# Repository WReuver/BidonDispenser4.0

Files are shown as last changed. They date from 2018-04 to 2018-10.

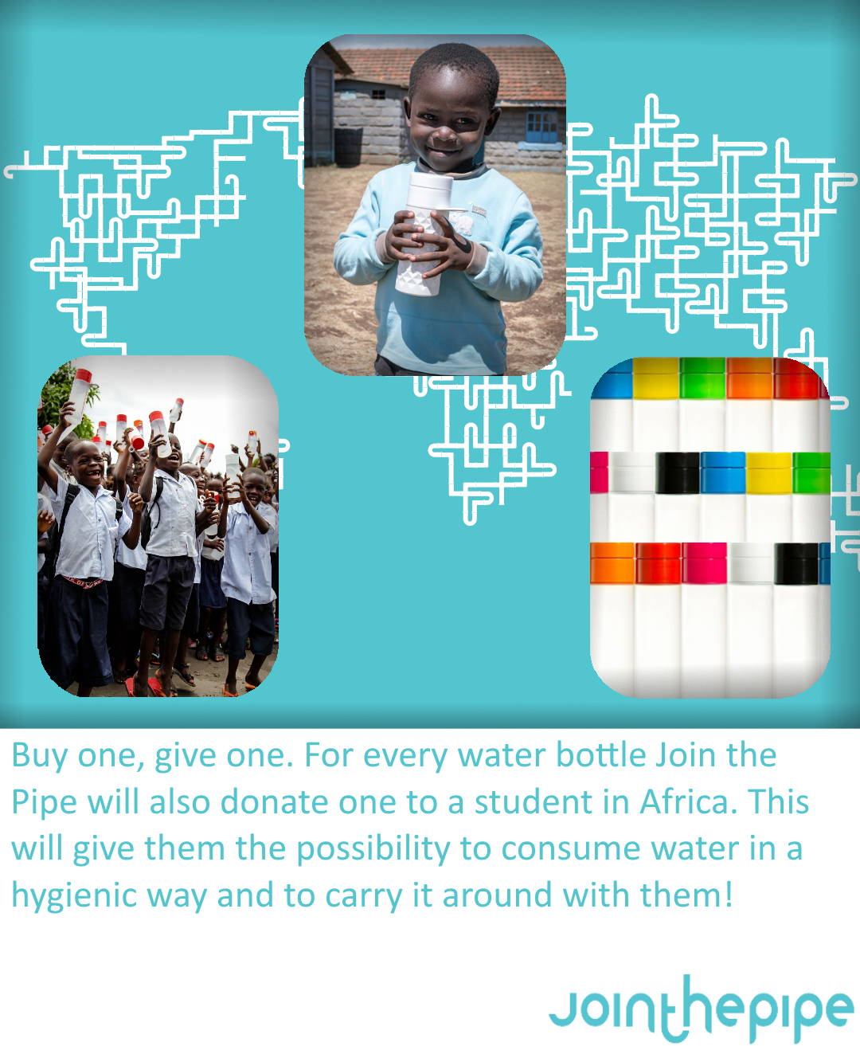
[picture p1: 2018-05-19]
RaspberryPi/Software/BidonDispenser/BidonDispenser/Assets/Images/Promotions/BuyOneGiveOne.png

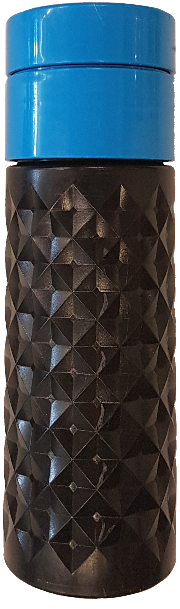
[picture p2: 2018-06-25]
RaspberryPi/Software/BidonDispenser/BidonDispenser/Assets/Images/BottleColours/B_BlueBottle.png

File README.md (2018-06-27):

# Bidon Dispenser 4.0
_Smart Solutions Semester - Join the Pipe - Year 17/18 - Semester 02_

### Authors
All the software is written by Robin C. Pel with student number 421 431. 
All the hardware is designed by Glen te Hofsté with student number 419 720. 

### Note to self
Use "git merge --allow-unrelated-histories [ORPHAN-BRANCH]" to merge orphan branches.

### While Loops
All the while loops in the Microcontroller's program:
- "./Communication/OneWire.cpp" line 13: Wait for a pin to be high
- "./Communication/USART.cpp" line 34: Wait for new data on the serial port
- "./Communication/USART.cpp" line 42: Wait for new data on the serial port for 2 seconds
- "./Hardware/SystemClock.cpp" line 13: Wait for the clock source to be ready
- "./Master/RaspberryPi.cpp" line 36: Wait until the pre-amble is found
- "./Sensors/DistanceSensor.cpp" line 93: Wait for a pin to be high
- "./Sensors/DistanceSensor.cpp" line 93: Wait for a pin to be low
- "./Sensors/TemperatureSensor.cpp" line 33: Wait for a pin to be high
- "./main.cpp" line 197, 280, 323, 362 and 384: Infinite loops

### Important
Not all code on the "microcontroller/software/develop" branch works with all the microcontroller hardware:  
	- All the commits **BEFORE** the tag "MCU_Festival" only work on the controller PCB v1.1  
	- All the commits **AFTER** the tag "MCU_Festival" only work on the controller PCB v2.0  
  
Another thing that's definitely worth mentioning is that on the microcontroller PCB v1.1 the ADC was used to read a 1 or 0.
This was done because for some weird reason it was not possible to read one of the digital pins, 
the microcontroller probably was broken or something but the decision was made to work around it for the time being.  
  
After the Smart Solutions Festival one of the distance sensors broke, this sensor was distance sensor number five.  
Distance Sensor Layout Layout (Top view, from the front):  
_Dist Sensor: [08] [01] [10] [03] [12] [05] [14] [07]_  
_Dist Sensor: [00] [09] [02] [11] [04] [13] [06] [15]_  

### Disclaimer
This was my first experience with C# and the Visual Studio IDE, there are probably a lot of things which could be optimized. 
This git repo was also misused a little bit, apologies. 
There is _no_ easter egg. 

### Regarding the UI Assets
All UI Assets were made using Paint dot net, you can get it here https://www.dotpdn.com/downloads/pdn.html

### The Team 💪
! The Team 💪

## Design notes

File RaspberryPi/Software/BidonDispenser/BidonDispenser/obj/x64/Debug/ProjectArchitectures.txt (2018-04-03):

C:\Git\BidonDispenser4.0\RaspberryPi\Software\BidonDispenser\BidonDispenser\BidonDispenser.csproj;x64

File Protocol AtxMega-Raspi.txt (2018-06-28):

==============================================================================================================================================
	Dictionary
==============================================================================================================================================
MASTER						= Raspberry Pi
SLAVE						= Micro Controller
LENGTH						= Length of the payload
COLUMNNUMBER 				= 0 ~ 7
EMPTY STATUS OF ALL COLUMNS	= 0b76543210, each bit indicates if a column is empty or not (0b00100111 => column 0, 1, 2 and 5 are empty)
NEW EMPTY DISTANCE			= From which distance the column will be seen as empty
LOWER TARGET TEMEPRATURE	= Which lower temperature the machine should aim for
==============================================================================================================================================

==============================================================================================================================================
	Protocol Format
==============================================================================================================================================
[PREAMBLE0] [PREAMBLE1] [COMMAND] [PARAMETER-LENGTH] [PARAMATERS]

PREAMBLE0			= 0x00
PREAMBLE1			= 0xFF
COMMAND				= See "Command Overview"
PARAMETER-LENGTH 	= Amount of parameters
PARAMATERS			= See "Command Overview"
==============================================================================================================================================

==============================================================================================================================================
	Command Overview
==============================================================================================================================================
COMMANDNAME: 		Lock
DESCRIPTION:		Locks all functionalities until unlocked
MASTER COMMAND:		[0x02]
MASTER PARAMETERS:	-
SLAVE COMMAND:		[0x03]
SLAVE PARAMETERS:	-

COMMANDNAME: 		Unlock
DESCRIPTION:		Unlocks all functionalities if locked
MASTER COMMAND:		[0x04]
MASTER PARAMETERS:	-
SLAVE COMMAND:		[0x05]
SLAVE PARAMETERS:	-

COMMANDNAME: 		Sense
DESCRIPTION:		A check used to sense whether the microcontroller is connected or not
MASTER COMMAND:		[0x06]
MASTER PARAMETERS:	-
SLAVE COMMAND:		[0x07]
SLAVE PARAMETERS:	[0xAB] [0xBC] [0xCD] [0xDA]

COMMANDNAME: 		Temperature
DESCRIPTION:		Command the slave to return the three temperature values
MASTER COMMAND:		[0x08]
MASTER PARAMATERS:	[LOWER TARGET TEMEPRATURE * 2]
SLAVE COMMAND:		[0x09]
SLAVE PARAMETERS:	[LOWER TEMPERATURE * 2] [MIDDLE TEMPERATURE * 2] [UPPER TEMPERATURE * 2]

COMMANDNAME: 		Dispense
DESCRIPTION:		Command the slave to dispense a bidon from the given column and to return the distance of the given column
MASTER COMMAND:		[0x0A]
MASTER PARAMETERS:	[COLUMN-NUMBER]
SLAVE COMMAND:		[0x0B]
SLAVE PARAMETERS:	[EMPTY STATUS OF ALL COLUMNS]

COMMANDNAME: 		Distance
DESCRIPTION:		Command the slave to return all column distances
MASTER COMMAND:		[0x0C]
MASTER PARAMETERS:	[NEW EMPTY DISTANCE (optional)]
SLAVE COMMAND:		[0x0D]
SLAVE PARAMETERS:	[EMPTY STATUS OF ALL COLUMNS]
==============================================================================================================================================

==============================================================================================================================================
	Slave Exceptions 
==============================================================================================================================================
ERRORNAME:			TimeOutError
SLAVE COMMAND:		[0xE0]
SLAVE PARAMETERS:	-

ERRORNAME:			UnknownCommandError
SLAVE COMMAND:		[0xE1]
SLAVE PARAMETERS:	-

ERRORNAME:			NotEnoughParameters
SLAVE COMMAND:		[0xE2]
SLAVE PARAMETERS:	-

ERRORNAME:			Locked
SLAVE COMMAND:		[0xE3]
SLAVE PARAMETERS:	-
==============================================================================================================================================

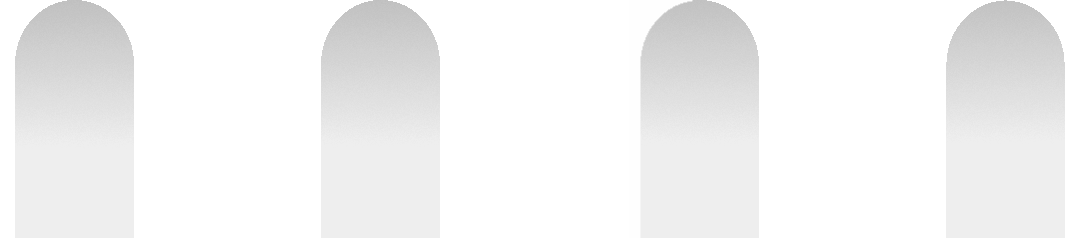
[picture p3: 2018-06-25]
RaspberryPi/Software/BidonDispenser/BidonDispenser/Assets/Images/Selections/FourBottleSelectionType1.png

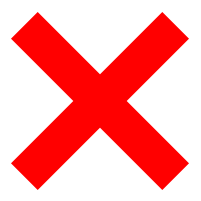
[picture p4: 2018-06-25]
RaspberryPi/Software/BidonDispenser/BidonDispenser/Assets/Images/Misc/RedX2.png

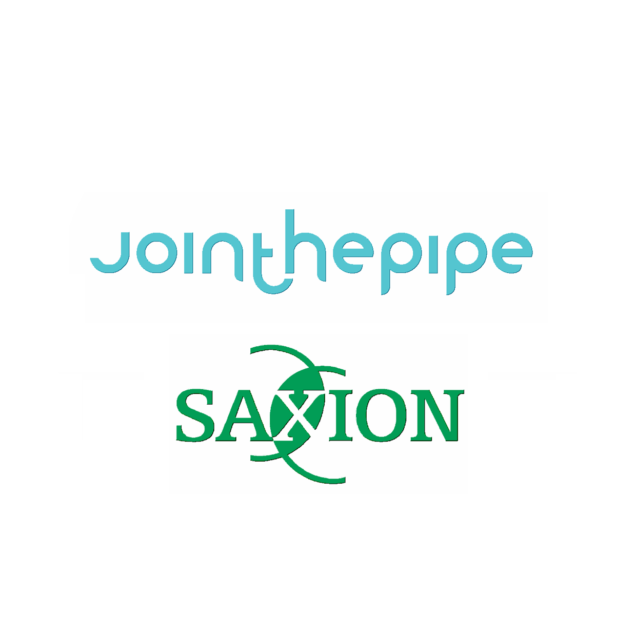
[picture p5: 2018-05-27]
RaspberryPi/Software/BidonDispenser/BidonDispenser/Assets/VisualAssets/LargeTile.scale-400.png

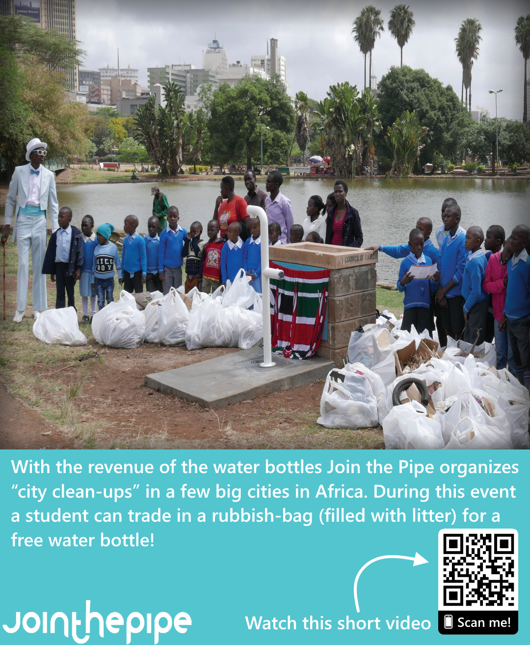
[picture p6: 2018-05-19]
RaspberryPi/Software/BidonDispenser/BidonDispenser/Assets/Images/Promotions/CleanUp.png

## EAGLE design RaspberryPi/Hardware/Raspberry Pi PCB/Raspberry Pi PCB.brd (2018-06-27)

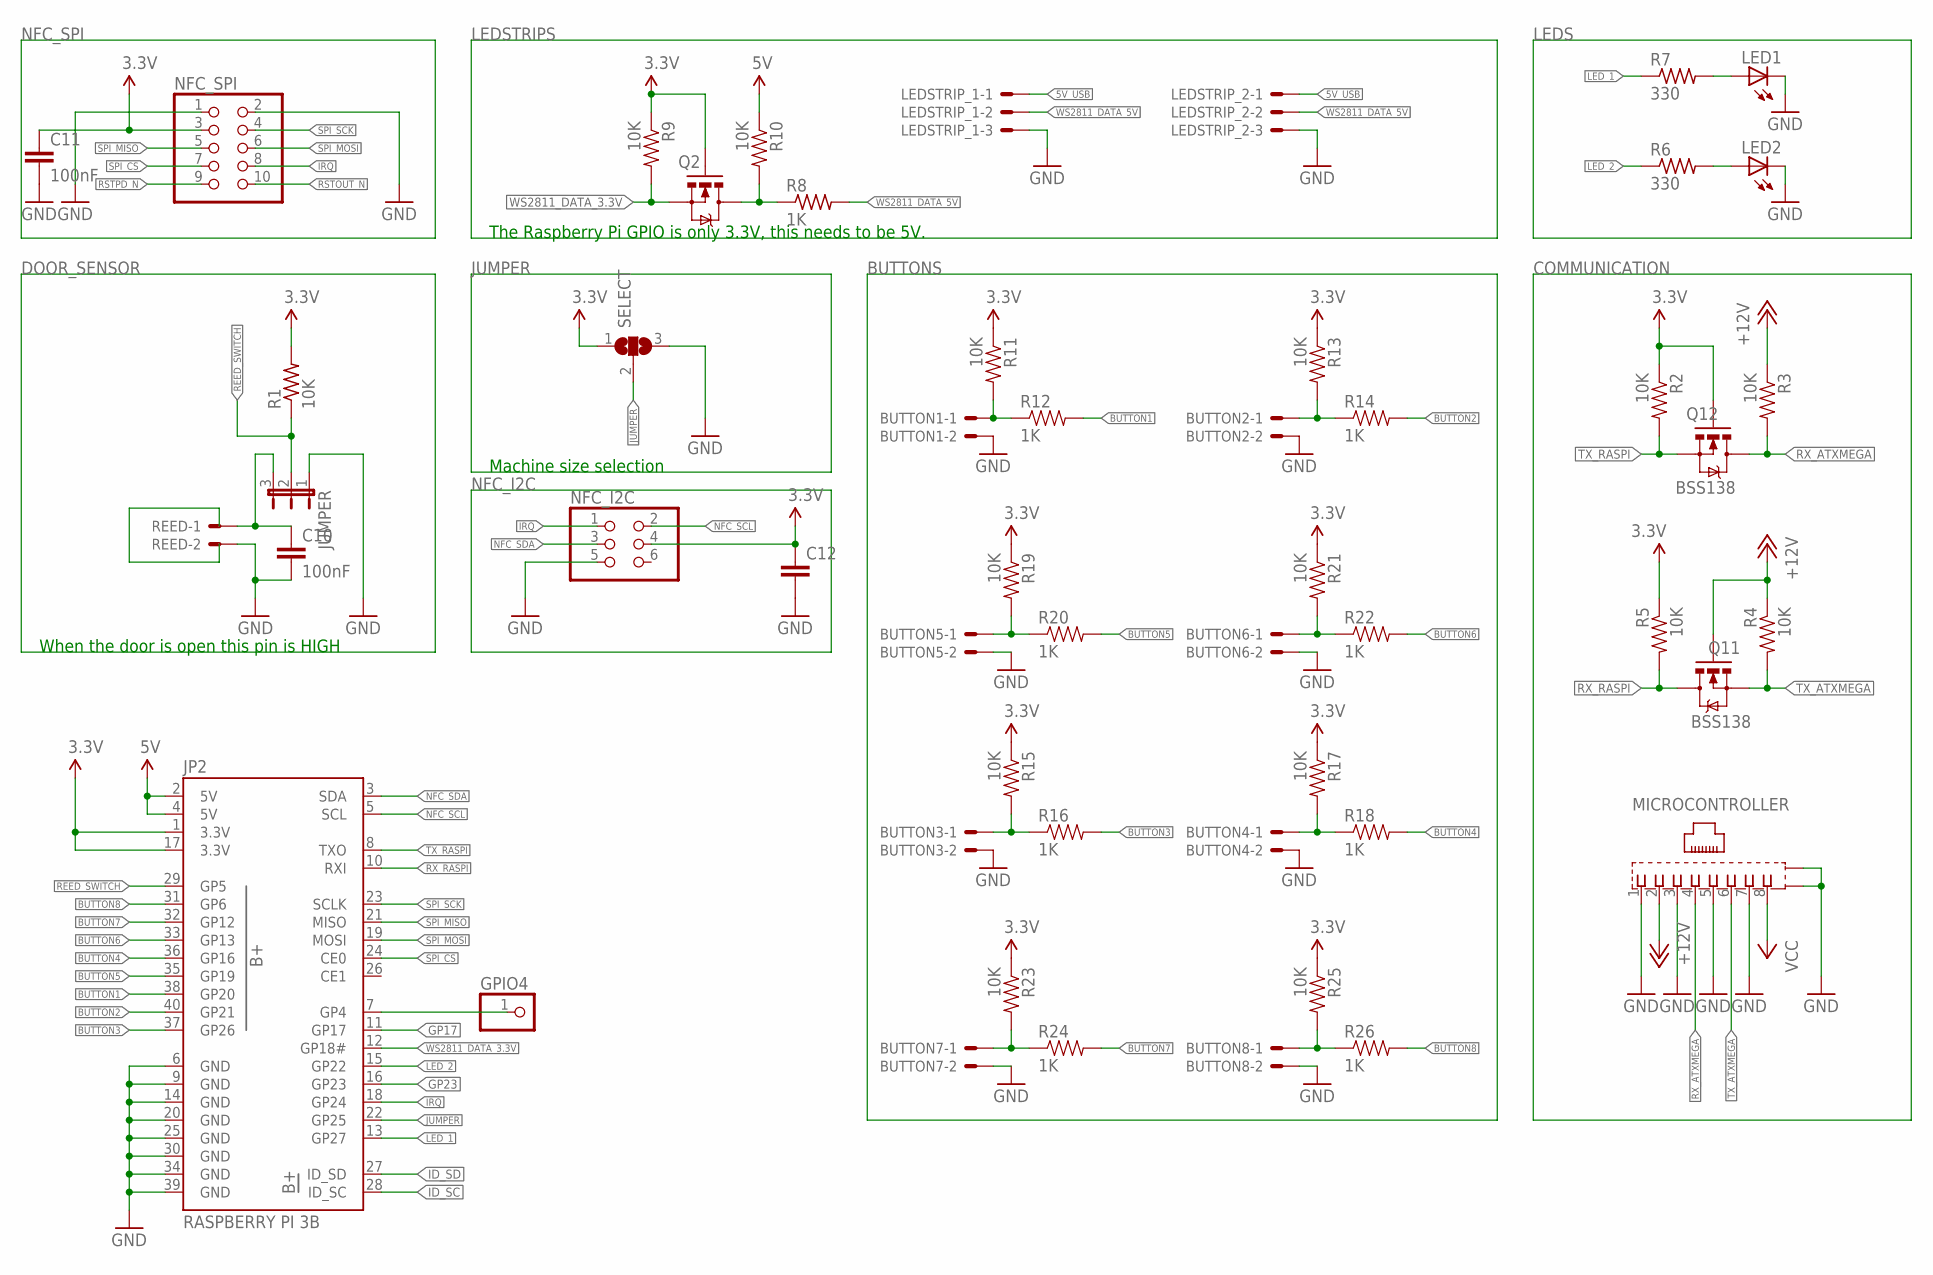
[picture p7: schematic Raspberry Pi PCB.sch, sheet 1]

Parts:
BUTTON1, BUTTON2, BUTTON3, BUTTON4, BUTTON5, BUTTON6, BUTTON7, BUTTON8: 22-05-7028-02; 7395-02
C10, C11, C12: 100nF; 0805
GPIO4: PINHD-1X1; 1X01
JP2: RASPBERRY PI 3B; 2X20-SHROUDED
JUMPER: JP2E; JP2
LED1, LED2: LEDCHIPLED_0805; CHIPLED_0805
LEDSTRIP_1, LEDSTRIP_2: 22-05-7038-03; 7395-03
MICROCONTROLLER: 0446200002
NFC_I2C: PINHD-2X3; 2X03
NFC_SPI: PINHD-2X5; 2X05
Q2, Q11, Q12: BSS138; SOT23-3
R1: 10K; R0805
R2, R3, R4, R5, R9, R10, R11, R13, R15, R17, R19, R21, R23, R25: 10K; 0603-RES
R6, R7: 330; R0805
R8: 1K; R0805
R12, R14, R16, R18, R20, R22, R24, R26: 1K; 0603-RES
REED: 22-05-7028-02; 7395-02
SELECT: SJ2W; SJ_2

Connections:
3.3V: C11.1, C12.1, JP2.1 (3.3V), JP2.17 (3.3V), NFC_I2C.4, NFC_SPI.3, Q2.1 (G), Q12.1 (G), R1.2, R2.1, R5.1, R9.1, R11.1, R13.1, R15.1, R17.1, R19.1, R21.1, R23.1, R25.1, SELECT.1
5V: JP2.2 (5V), JP2.4 (5V), R10.1; also elsewhere on the board
5V_USB: LEDSTRIP_1.1, LEDSTRIP_2.1; also elsewhere on the board
+12V: MICROCONTROLLER.2, Q11.1 (G), R3.1, R4.1
BUTTON1: JP2.38 (GP20), R12.2
BUTTON2: JP2.40 (GP21), R14.2
BUTTON3: JP2.37 (GP26), R16.2
BUTTON4: JP2.36 (GP16), R18.2
BUTTON5: JP2.35 (GP19), R20.2
BUTTON6: JP2.33 (GP13), R22.2
BUTTON7: JP2.32 (GP12), R24.2
BUTTON8: JP2.31 (GP6), R26.2
GND: BUTTON1.2, BUTTON2.2, BUTTON3.2, BUTTON4.2, BUTTON5.2, BUTTON6.2, BUTTON7.2, BUTTON8.2, C10.2, C11.2, C12.2, JP2.6 (GND), JP2.9 (GND), JP2.14 (GND), JP2.20 (GND), JP2.25 (GND), JP2.30 (GND), JP2.34 (GND), JP2.39 (GND), JUMPER.1, LED1.C, LED2.C, LEDSTRIP_1.3, LEDSTRIP_2.3, MICROCONTROLLER.1, MICROCONTROLLER.3, MICROCONTROLLER.5, MICROCONTROLLER.7, MICROCONTROLLER.S@1 (S1), MICROCONTROLLER.S@2 (S2), NFC_I2C.5, NFC_SPI.1, NFC_SPI.2, REED.2, SELECT.3; also elsewhere on the board
GP4: GPIO4.1, JP2.7 (GP4)
GP17: JP2.11 (GP17)
GP23: JP2.16 (GP23)
ID_SC: JP2.28 (ID_SC)
ID_SD: JP2.27 (ID_SD)
IRQ: JP2.18 (GP24), NFC_I2C.1, NFC_SPI.8
JUMPER: JP2.22 (GP25), SELECT.2
LED_1: JP2.13 (GP27), R7.1
LED_2: JP2.15 (GP22), R6.1
unnamed: C10.1, JUMPER.3, REED.1
unnamed: BUTTON2.1, R13.2, R14.1
unnamed: Q2.3 (D), R8.1, R10.2
unnamed: LED2.A, R6.2
unnamed: LED1.A, R7.2
unnamed: BUTTON1.1, R11.2, R12.1
unnamed: BUTTON3.1, R15.2, R16.1
unnamed: BUTTON4.1, R17.2, R18.1
unnamed: BUTTON5.1, R19.2, R20.1
unnamed: BUTTON6.1, R21.2, R22.1
unnamed: BUTTON7.1, R23.2, R24.1
unnamed: BUTTON8.1, R25.2, R26.1
NFC_SCL: JP2.5 (SCL), NFC_I2C.2
NFC_SDA: JP2.3 (SDA), NFC_I2C.3
REED_SWITCH: JP2.29 (GP5), JUMPER.2, R1.1
RSTOUT_N: NFC_SPI.10
RSTPD_N: NFC_SPI.9
RX_ATXMEGA: MICROCONTROLLER.4, Q12.3 (D), R3.2
RX_RASPI: JP2.10 (RXI), Q11.3 (D), R5.2
SPI_CS: JP2.24 (CE0), NFC_SPI.7
SPI_MISO: JP2.21 (MISO), NFC_SPI.5
SPI_MOSI: JP2.19 (MOSI), NFC_SPI.6
SPI_SCK: JP2.23 (SCLK), NFC_SPI.4
TX_ATXMEGA: MICROCONTROLLER.6, Q11.2 (S), R4.2
TX_RASPI: JP2.8 (TXO), Q12.2 (S), R2.2
VCC: MICROCONTROLLER.8
WS2811_DATA_3.3V: JP2.12 (GP18#), Q2.2 (S), R9.2
WS2811_DATA_5V: LEDSTRIP_1.2, LEDSTRIP_2.2, R8.2

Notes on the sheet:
Machine size selection
When the door is open this pin is HIGH
The Raspberry Pi GPIO is only 3.3V, this needs to be 5V.

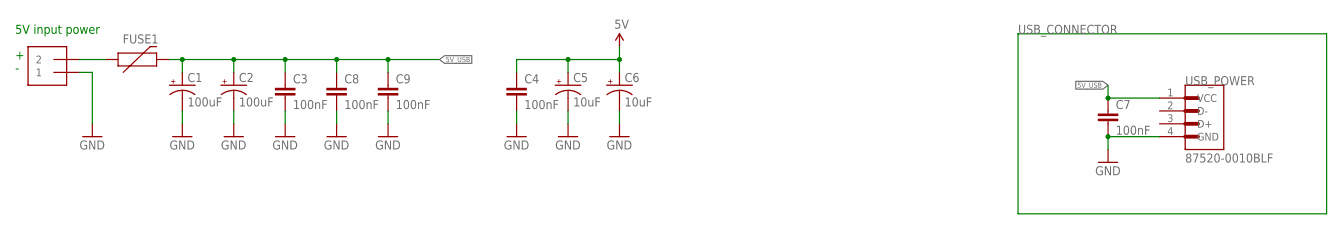
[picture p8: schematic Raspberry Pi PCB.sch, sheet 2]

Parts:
C1, C2: 100uF; 175TMP-0810
C3, C4, C7, C8, C9: 100nF; 0805
C5, C6: 10uF; 153CLV-0505
FUSE1: 6V/0.5A; 1206
INPUT: 1X2-3.5MM
USB_POWER: 87520-0010BLF; FCI_87520-0010BLF

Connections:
5V: C4.1, C5.+, C6.+; also elsewhere on the board
5V_USB: C1.+, C2.+, C3.1, C7.1, C8.1, C9.1, FUSE1.2, USB_POWER.1 (VCC); also elsewhere on the board
GND: C1.-, C2.-, C3.2, C4.2, C5.-, C6.-, C7.2, C8.2, C9.2, INPUT.1, USB_POWER.4 (GND); also elsewhere on the board
VIN1: FUSE1.1, INPUT.2

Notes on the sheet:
5V input power

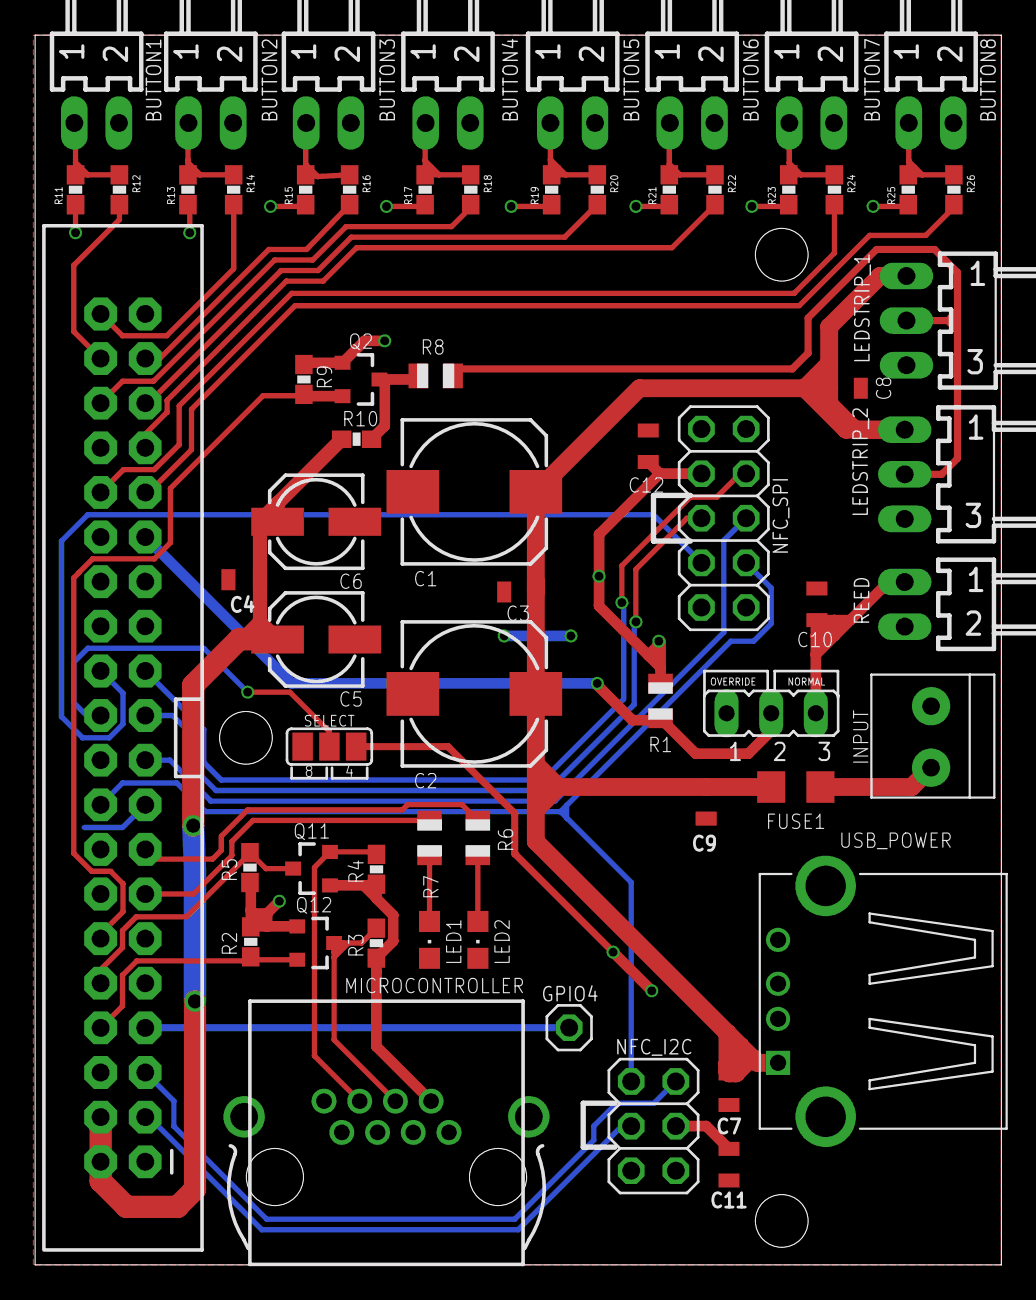
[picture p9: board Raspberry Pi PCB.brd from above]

Board: 2 copper layers, 55.0 x 70.0 mm, 64 parts (0 on the bottom side), 44 nets.

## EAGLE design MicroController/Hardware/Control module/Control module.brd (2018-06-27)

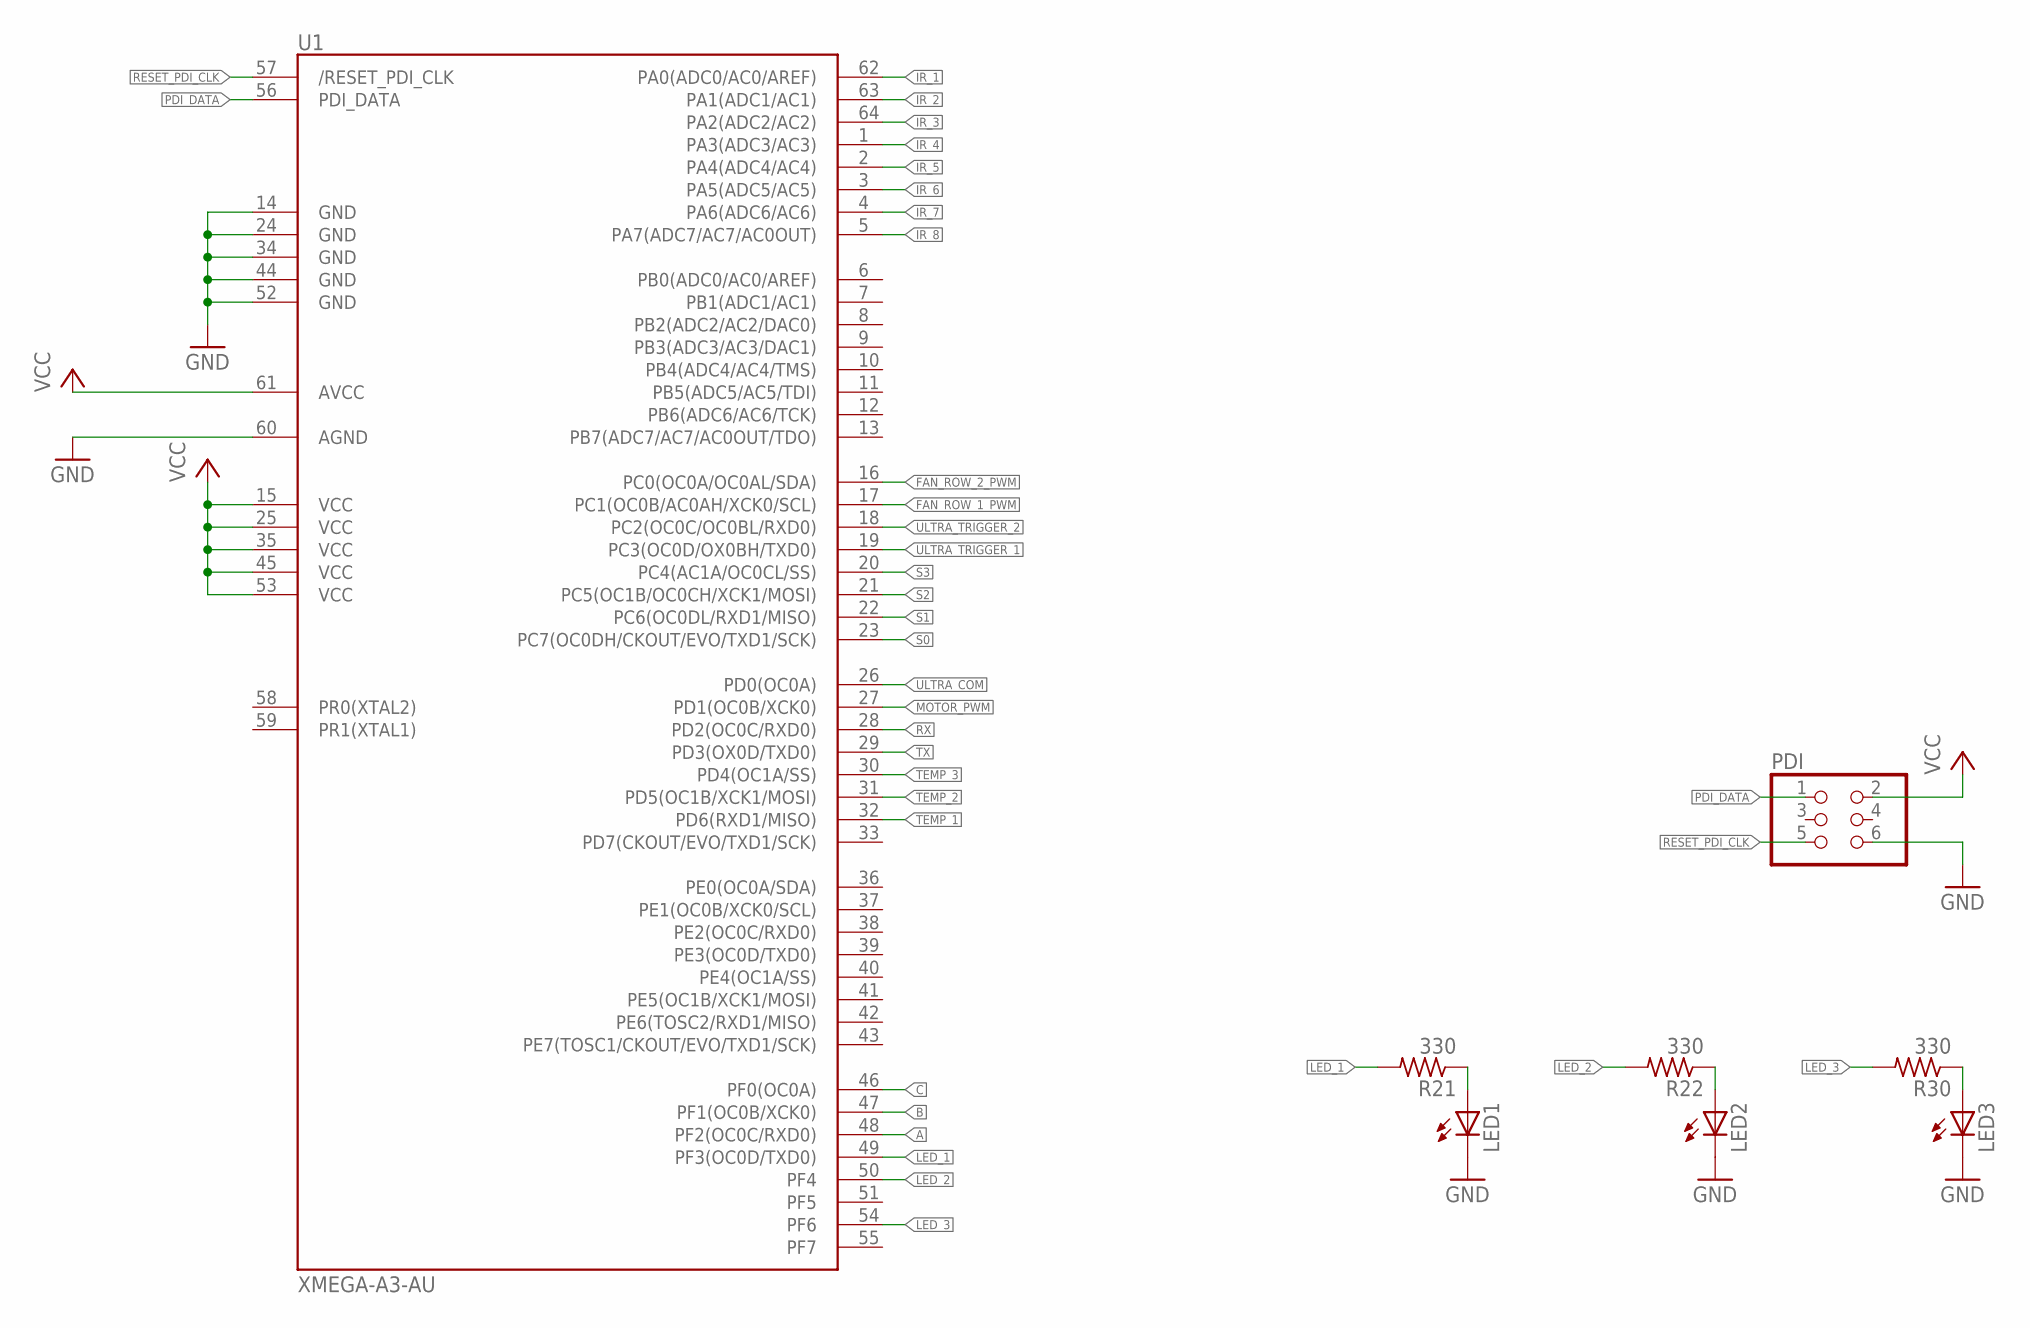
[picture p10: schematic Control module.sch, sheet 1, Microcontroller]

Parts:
LED1, LED2, LED3: LEDCHIPLED_0805; CHIPLED_0805
PDI: PINHD-2X3; 2X03
R21, R22, R30: 330; R0805
U1: XMEGA-A3-AU; TQFP64_14X14MM_MCU

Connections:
A: U1.48 (PF2(OC0C/RXD0)); also elsewhere on the board
B: U1.47 (PF1(OC0B/XCK0)); also elsewhere on the board
C: U1.46 (PF0(OC0A)); also elsewhere on the board
FAN_ROW_1_PWM: U1.17 (PC1(OC0B/AC0AH/XCK0/SCL)); also elsewhere on the board
FAN_ROW_2_PWM: U1.16 (PC0(OC0A/OC0AL/SDA)); also elsewhere on the board
GND: LED1.C, LED2.C, LED3.C, PDI.6, U1.14 (GND1), U1.24 (GND2), U1.34 (GND3), U1.44 (GND4), U1.52 (GND5), U1.60 (AGND); also elsewhere on the board
IR_1: U1.62 (PA0(ADC0/AC0/AREF)); also elsewhere on the board
IR_2: U1.63 (PA1(ADC1/AC1)); also elsewhere on the board
IR_3: U1.64 (PA2(ADC2/AC2)); also elsewhere on the board
IR_4: U1.1 (PA3(ADC3/AC3)); also elsewhere on the board
IR_5: U1.2 (PA4(ADC4/AC4)); also elsewhere on the board
IR_6: U1.3 (PA5(ADC5/AC5)); also elsewhere on the board
IR_7: U1.4 (PA6(ADC6/AC6)); also elsewhere on the board
IR_8: U1.5 (PA7(ADC7/AC7/AC0OUT)); also elsewhere on the board
LED_1: R21.2, U1.49 (PF3(OC0D/TXD0))
LED_2: R22.2, U1.50 (PF4)
LED_3: R30.2, U1.54 (PF6)
MOTOR_PWM: U1.27 (PD1(OC0B/XCK0)); also elsewhere on the board
unnamed: LED2.A, R22.1
unnamed: LED1.A, R21.1
unnamed: LED3.A, R30.1
PDI_DATA: PDI.1, U1.56 (PDI_DATA)
RESET_PDI_CLK: PDI.5, U1.57 (/RESET_PDI_CLK)
RX: U1.28 (PD2(OC0C/RXD0)); also elsewhere on the board
S0: U1.23 (PC7(OC0DH/CKOUT/EVO/TXD1/SCK)); also elsewhere on the board
S1: U1.22 (PC6(OC0DL/RXD1/MISO)); also elsewhere on the board
S2: U1.21 (PC5(OC1B/OC0CH/XCK1/MOSI)); also elsewhere on the board
S3: U1.20 (PC4(AC1A/OC0CL/SS)); also elsewhere on the board
TEMP_1: U1.32 (PD6(RXD1/MISO)); also elsewhere on the board
TEMP_2: U1.31 (PD5(OC1B/XCK1/MOSI)); also elsewhere on the board
TEMP_3: U1.30 (PD4(OC1A/SS)); also elsewhere on the board
TX: U1.29 (PD3(OX0D/TXD0)); also elsewhere on the board
ULTRA_COM: U1.26 (PD0(OC0A)); also elsewhere on the board
ULTRA_TRIGGER_1: U1.19 (PC3(OC0D/OX0BH/TXD0)); also elsewhere on the board
ULTRA_TRIGGER_2: U1.18 (PC2(OC0C/OC0BL/RXD0)); also elsewhere on the board
VCC: PDI.2, U1.15 (VCC1), U1.25 (VCC2), U1.35 (VCC3), U1.45 (VCC4), U1.53 (VCC5), U1.61 (AVCC); also elsewhere on the board

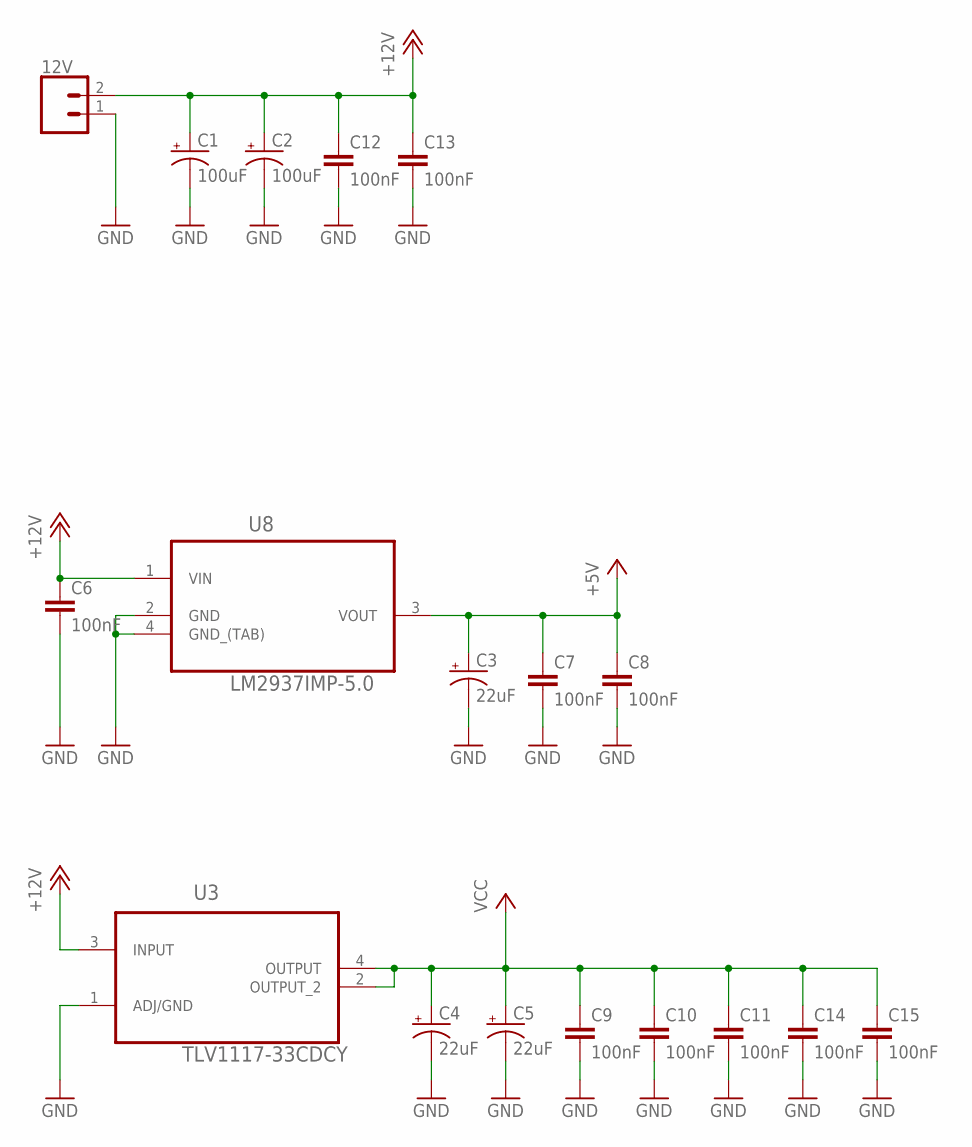
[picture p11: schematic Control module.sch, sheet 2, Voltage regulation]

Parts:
12V: CONN_025MM; SCREWTERMINAL-5MM-2
C1, C2: 100uF; 150CLZ-0810
C3, C4, C5: 22uF; 153CLV-0505
C6, C7, C8, C9, C10, C11, C12, C13, C14, C15: 100nF; 0805
U3: TLV1117-33CDCY; SOT230P700X180-4N
U8: LM2937IMP-5.0; SOT230P700X180-4N

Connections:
+5V: C3.+, C7.1, C8.1, U8.3 (VOUT); also elsewhere on the board
+12V: 12V.2, C1.+, C2.+, C6.1, C12.1, C13.1, U3.3 (INPUT), U8.1 (VIN); also elsewhere on the board
GND: 12V.1, C1.-, C2.-, C3.-, C4.-, C5.-, C6.2, C7.2, C8.2, C9.2, C10.2, C11.2, C12.2, C13.2, C14.2, C15.2, U3.1 (ADJ/GND), U8.2 (GND), U8.4 (GND_(TAB)); also elsewhere on the board
VCC: C4.+, C5.+, C9.1, C10.1, C11.1, C14.1, C15.1, U3.2 (OUTPUT_2), U3.4 (OUTPUT); also elsewhere on the board

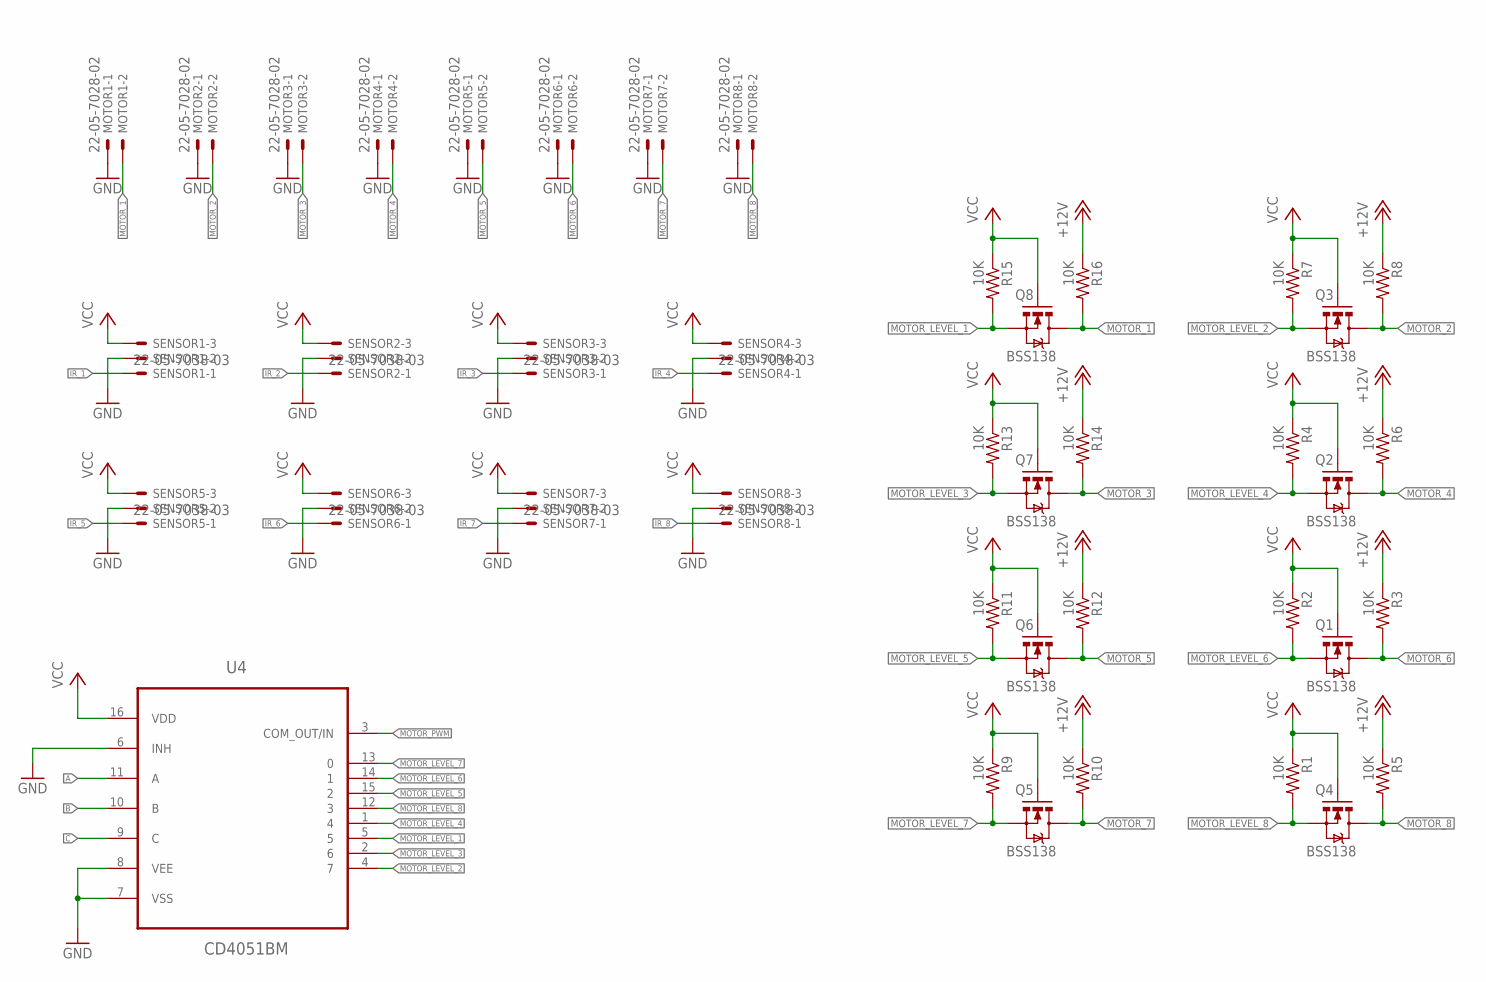
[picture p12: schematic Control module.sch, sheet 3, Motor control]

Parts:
MOTOR1, MOTOR2, MOTOR3, MOTOR4, MOTOR5, MOTOR6, MOTOR7, MOTOR8: 22-05-7028-02; 7395-02
Q1, Q2, Q3, Q4, Q5, Q6, Q7, Q8: BSS138; SOT23-3
R1, R2, R3, R4, R5, R6, R7, R8, R9, R10, R11, R12, R13, R14, R15, R16: 10K; 0603-RES
SENSOR1, SENSOR2, SENSOR3, SENSOR4, SENSOR5, SENSOR6, SENSOR7, SENSOR8: 22-05-7038-03; 7395-03
U4: CD4051BM; SOIC127P600X175-16N

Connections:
+12V: R3.1, R5.1, R6.1, R8.1, R10.1, R12.1, R14.1, R16.1; also elsewhere on the board
A: U4.11 (A); also elsewhere on the board
B: U4.10 (B); also elsewhere on the board
C: U4.9 (C); also elsewhere on the board
GND: MOTOR1.1, MOTOR2.1, MOTOR3.1, MOTOR4.1, MOTOR5.1, MOTOR6.1, MOTOR7.1, MOTOR8.1, SENSOR1.2, SENSOR2.2, SENSOR3.2, SENSOR4.2, SENSOR5.2, SENSOR6.2, SENSOR7.2, SENSOR8.2, U4.6 (INH), U4.7 (VSS), U4.8 (VEE); also elsewhere on the board
IR_1: SENSOR1.1; also elsewhere on the board
IR_2: SENSOR2.1; also elsewhere on the board
IR_3: SENSOR3.1; also elsewhere on the board
IR_4: SENSOR4.1; also elsewhere on the board
IR_5: SENSOR5.1; also elsewhere on the board
IR_6: SENSOR6.1; also elsewhere on the board
IR_7: SENSOR7.1; also elsewhere on the board
IR_8: SENSOR8.1; also elsewhere on the board
MOTOR_1: MOTOR1.2, Q8.3 (D), R16.2
MOTOR_2: MOTOR2.2, Q3.3 (D), R8.2
MOTOR_3: MOTOR3.2, Q7.3 (D), R14.2
MOTOR_4: MOTOR4.2, Q2.3 (D), R6.2
MOTOR_5: MOTOR5.2, Q6.3 (D), R12.2
MOTOR_6: MOTOR6.2, Q1.3 (D), R3.2
MOTOR_7: MOTOR7.2, Q5.3 (D), R10.2
MOTOR_8: MOTOR8.2, Q4.3 (D), R5.2
MOTOR_LEVEL_1: Q8.2 (S), R15.2, U4.5
MOTOR_LEVEL_2: Q3.2 (S), R7.2, U4.4 (7)
MOTOR_LEVEL_3: Q7.2 (S), R13.2, U4.2 (6)
MOTOR_LEVEL_4: Q2.2 (S), R4.2, U4.1 (4)
MOTOR_LEVEL_5: Q6.2 (S), R11.2, U4.15 (2)
MOTOR_LEVEL_6: Q1.2 (S), R2.2, U4.14 (1)
MOTOR_LEVEL_7: Q5.2 (S), R9.2, U4.13 (0)
MOTOR_LEVEL_8: Q4.2 (S), R1.2, U4.12 (3)
MOTOR_PWM: U4.3 (COM_OUT/IN); also elsewhere on the board
VCC: Q1.1 (G), Q2.1 (G), Q3.1 (G), Q4.1 (G), Q5.1 (G), Q6.1 (G), Q7.1 (G), Q8.1 (G), R1.1, R2.1, R4.1, R7.1, R9.1, R11.1, R13.1, R15.1, SENSOR1.3, SENSOR2.3, SENSOR3.3, SENSOR4.3, SENSOR5.3, SENSOR6.3, SENSOR7.3, SENSOR8.3, U4.16 (VDD); also elsewhere on the board

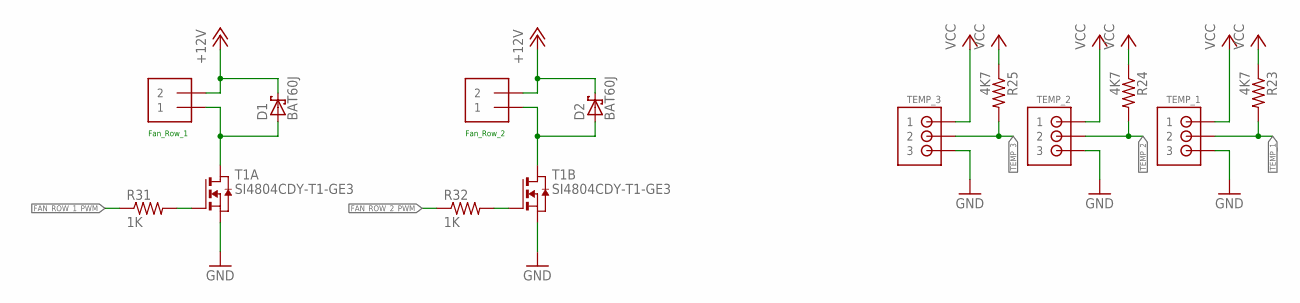
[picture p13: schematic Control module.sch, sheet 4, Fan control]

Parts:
D1, D2: BAT60J; SOD323_ST
FAN_1, FAN_2: 1X2-3.5MM
R23, R24, R25: 4K7; R0805
R31, R32: 1K; 0603-RES
T1: SI4804CDY-T1-GE3; SO8
TEMP_1, TEMP_2, TEMP_3: JST-PH_3-PIN_HEADER; JST_B3B-PH_HEADER

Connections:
+12V: D1.C, D2.C, FAN_1.2, FAN_2.2; also elsewhere on the board
FAN_ROW_1_PWM: R31.1; also elsewhere on the board
FAN_ROW_2_PWM: R32.1; also elsewhere on the board
GND: T1.1 (S), T1.3 (S), TEMP_1.P3 (3), TEMP_2.P3 (3), TEMP_3.P3 (3); also elsewhere on the board
unnamed: R31.2, T1.2 (G)
unnamed: D2.A, FAN_2.1, T1.5 (D), T1.6 (D)
unnamed: R32.2, T1.4 (G)
unnamed: D1.A, FAN_1.1, T1.7 (D), T1.8 (D)
TEMP_1: R23.2, TEMP_1.P2 (2); also elsewhere on the board
TEMP_2: R24.2, TEMP_2.P2 (2); also elsewhere on the board
TEMP_3: R25.2, TEMP_3.P2 (2); also elsewhere on the board
VCC: R23.1, R24.1, R25.1, TEMP_1.P1 (1), TEMP_2.P1 (1), TEMP_3.P1 (1); also elsewhere on the board

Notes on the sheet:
Fan_Row_2
Fan_Row_1

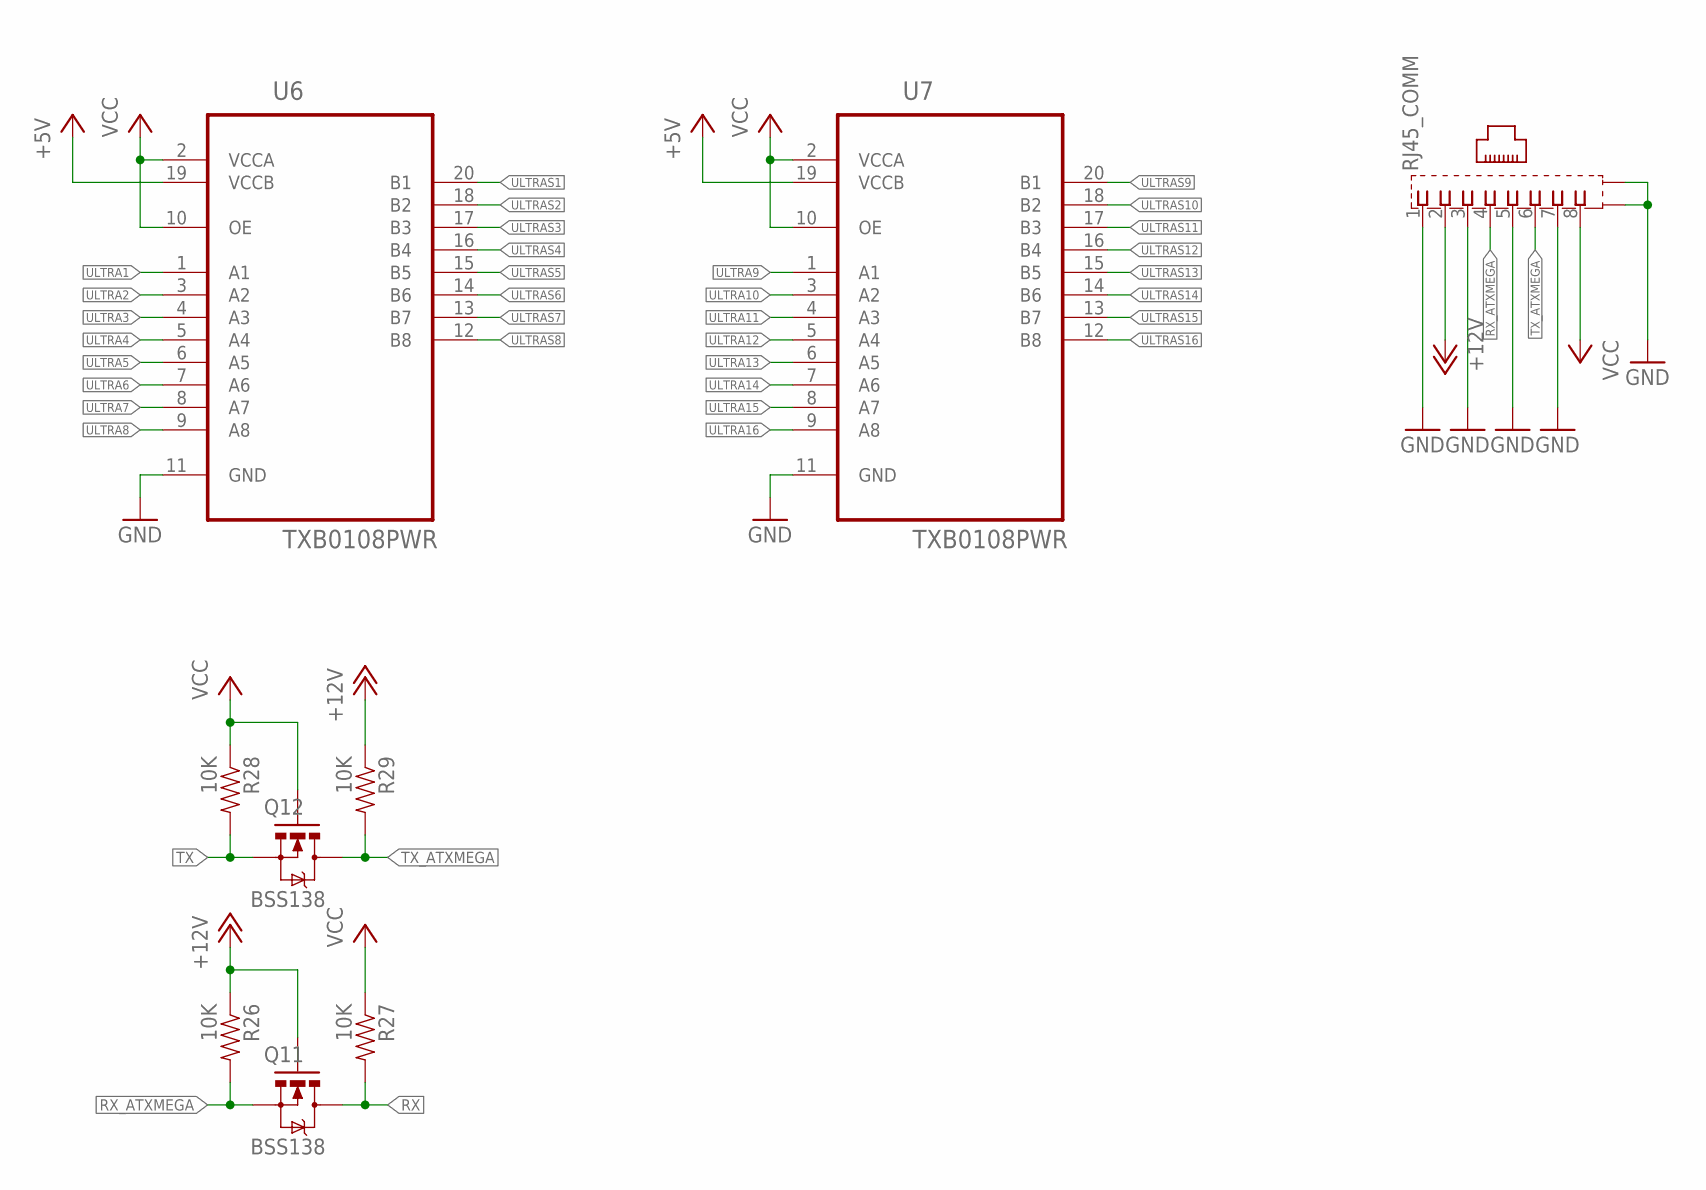
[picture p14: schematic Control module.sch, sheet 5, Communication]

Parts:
Q11, Q12: BSS138; SOT23-3
R26, R27, R28, R29: 10K; 0603-RES
RJ45_COMM: 0446200002
U6, U7: TXB0108PWR; SOP65P640X120-20N

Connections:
+5V: U6.19 (VCCB), U7.19 (VCCB); also elsewhere on the board
+12V: Q11.1 (G), R26.1, R29.1, RJ45_COMM.2; also elsewhere on the board
GND: RJ45_COMM.1, RJ45_COMM.3, RJ45_COMM.5, RJ45_COMM.7, RJ45_COMM.S@1 (S1), RJ45_COMM.S@2 (S2), U6.11 (GND), U7.11 (GND); also elsewhere on the board
RX: Q11.3 (D), R27.2; also elsewhere on the board
RX_ATXMEGA: Q11.2 (S), R26.2, RJ45_COMM.4
TX: Q12.2 (S), R28.2; also elsewhere on the board
TX_ATXMEGA: Q12.3 (D), R29.2, RJ45_COMM.6
ULTRA1: U6.1 (A1); also elsewhere on the board
ULTRA2: U6.3 (A2); also elsewhere on the board
ULTRA3: U6.4 (A3); also elsewhere on the board
ULTRA4: U6.5 (A4); also elsewhere on the board
ULTRA5: U6.6 (A5); also elsewhere on the board
ULTRA6: U6.7 (A6); also elsewhere on the board
ULTRA7: U6.8 (A7); also elsewhere on the board
ULTRA8: U6.9 (A8); also elsewhere on the board
ULTRA9: U7.1 (A1); also elsewhere on the board
ULTRA10: U7.3 (A2); also elsewhere on the board
ULTRA11: U7.4 (A3); also elsewhere on the board
ULTRA12: U7.5 (A4); also elsewhere on the board
ULTRA13: U7.6 (A5); also elsewhere on the board
ULTRA14: U7.7 (A6); also elsewhere on the board
ULTRA15: U7.8 (A7); also elsewhere on the board
ULTRA16: U7.9 (A8); also elsewhere on the board
ULTRAS1: U6.20 (B1); also elsewhere on the board
ULTRAS2: U6.18 (B2); also elsewhere on the board
ULTRAS3: U6.17 (B3); also elsewhere on the board
ULTRAS4: U6.16 (B4); also elsewhere on the board
ULTRAS5: U6.15 (B5); also elsewhere on the board
ULTRAS6: U6.14 (B6); also elsewhere on the board
ULTRAS7: U6.13 (B7); also elsewhere on the board
ULTRAS8: U6.12 (B8); also elsewhere on the board
ULTRAS9: U7.20 (B1); also elsewhere on the board
ULTRAS10: U7.18 (B2); also elsewhere on the board
ULTRAS11: U7.17 (B3); also elsewhere on the board
ULTRAS12: U7.16 (B4); also elsewhere on the board
ULTRAS13: U7.15 (B5); also elsewhere on the board
ULTRAS14: U7.14 (B6); also elsewhere on the board
ULTRAS15: U7.13 (B7); also elsewhere on the board
ULTRAS16: U7.12 (B8); also elsewhere on the board
VCC: Q12.1 (G), R27.1, R28.1, RJ45_COMM.8, U6.2 (VCCA), U6.10 (OE), U7.2 (VCCA), U7.10 (OE); also elsewhere on the board

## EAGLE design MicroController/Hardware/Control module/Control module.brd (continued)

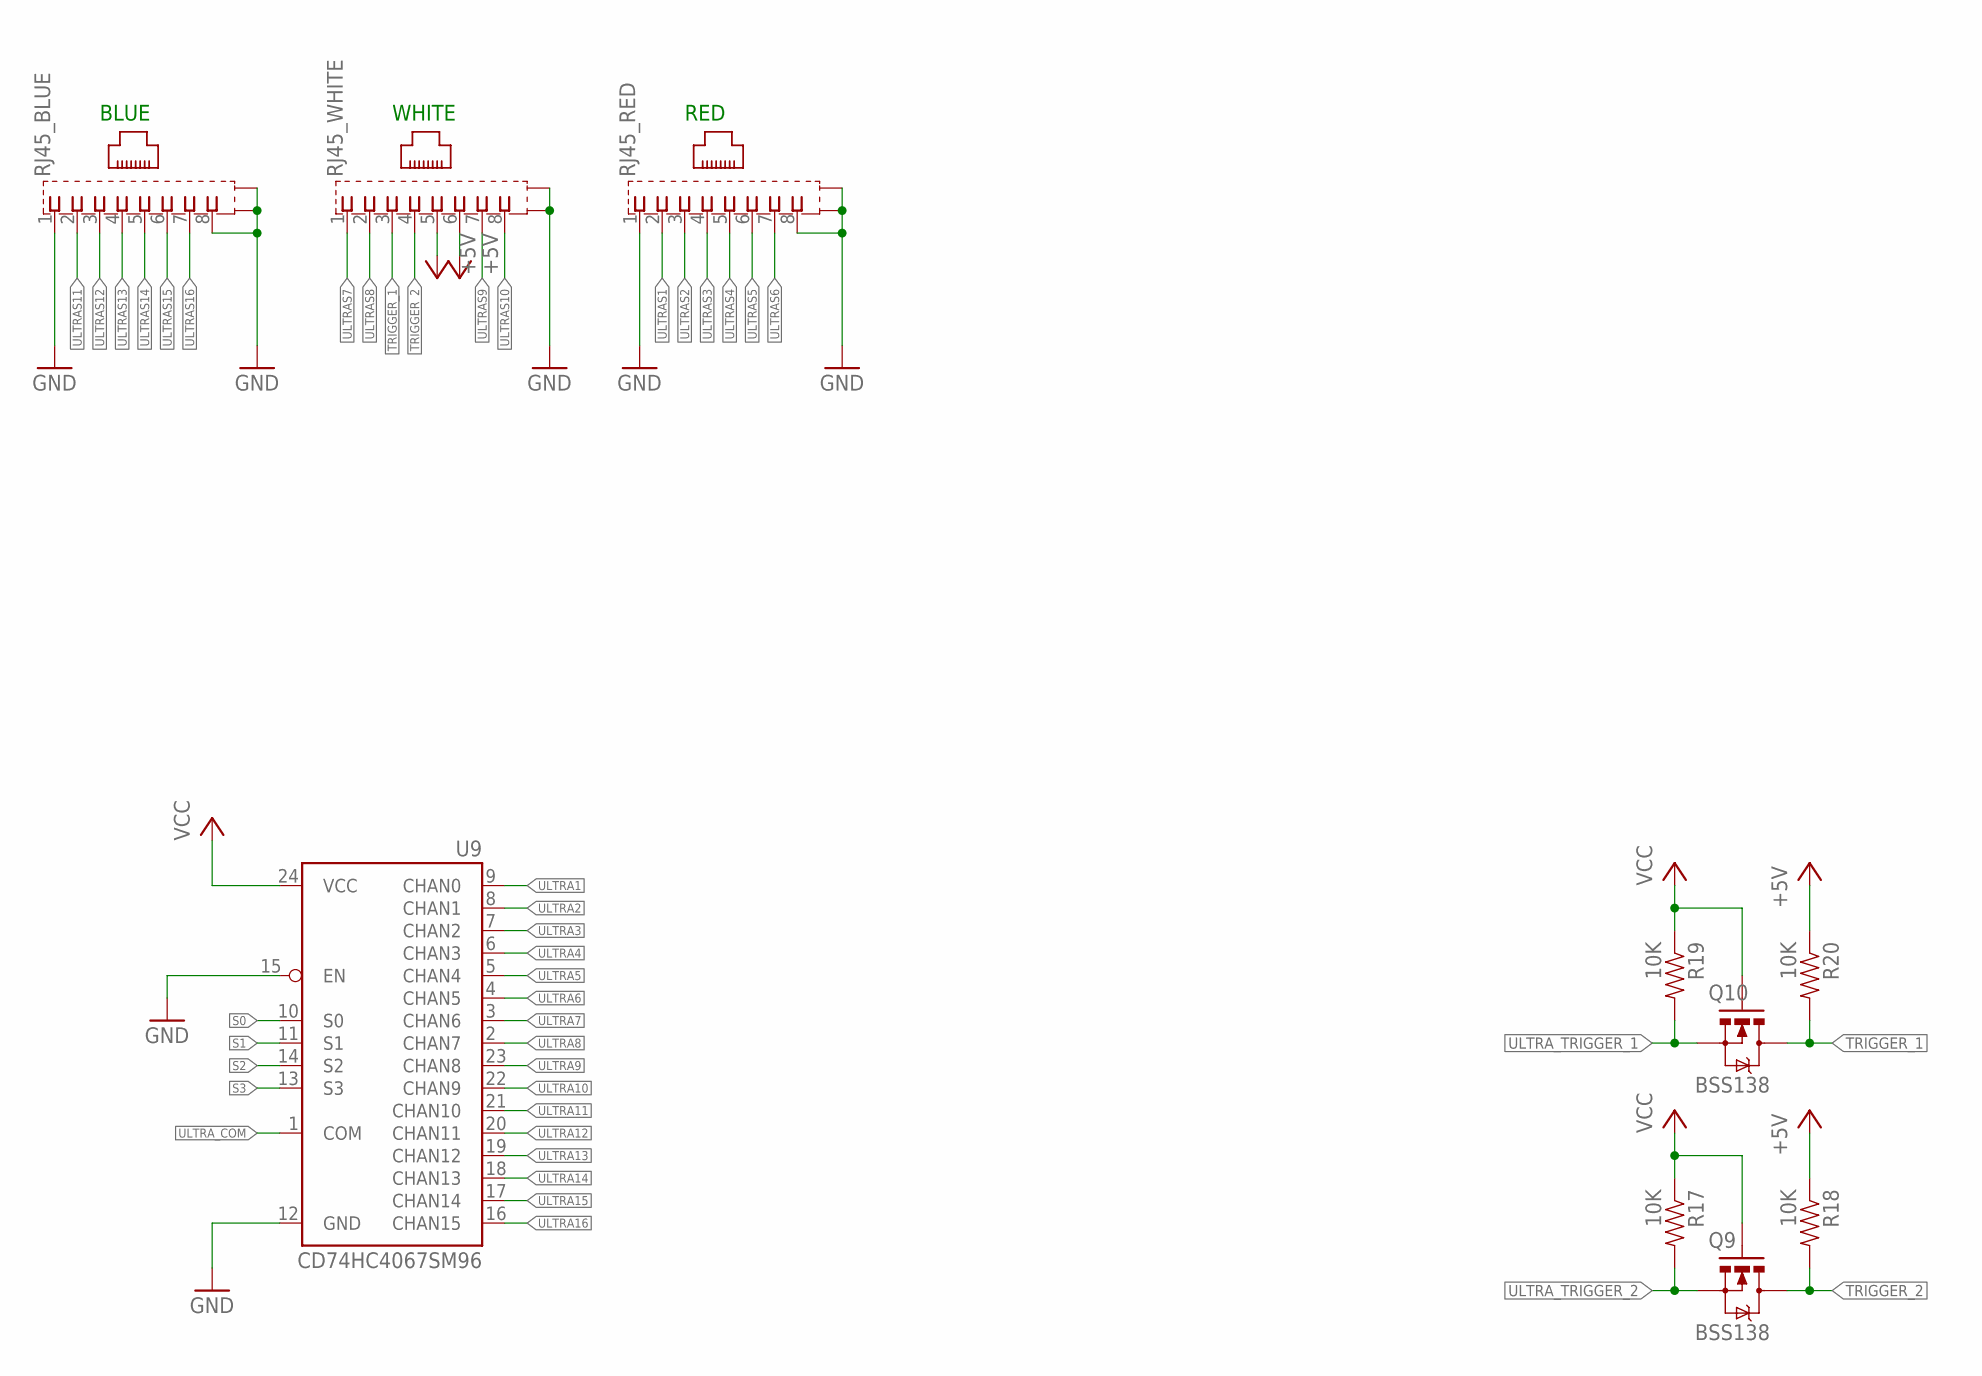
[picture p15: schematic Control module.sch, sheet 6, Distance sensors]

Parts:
Q9, Q10: BSS138; SOT23-3
R17, R18, R19, R20: 10K; 0603-RES
RJ45_BLUE, RJ45_RED, RJ45_WHITE: 0446200002
U9: CD74HC4067SM96; SSOP24

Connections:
+5V: R18.1, R20.1, RJ45_WHITE.5, RJ45_WHITE.6; also elsewhere on the board
GND: RJ45_BLUE.1, RJ45_BLUE.8, RJ45_BLUE.S@1 (S1), RJ45_BLUE.S@2 (S2), RJ45_RED.1, RJ45_RED.8, RJ45_RED.S@1 (S1), RJ45_RED.S@2 (S2), RJ45_WHITE.S@1 (S1), RJ45_WHITE.S@2 (S2), U9.12 (GND), U9.15 (EN); also elsewhere on the board
S0: U9.10 (S0); also elsewhere on the board
S1: U9.11 (S1); also elsewhere on the board
S2: U9.14 (S2); also elsewhere on the board
S3: U9.13 (S3); also elsewhere on the board
TRIGGER_1: Q10.3 (D), R20.2, RJ45_WHITE.3
TRIGGER_2: Q9.3 (D), R18.2, RJ45_WHITE.4
ULTRA1: U9.9 (CHAN0); also elsewhere on the board
ULTRA2: U9.8 (CHAN1); also elsewhere on the board
ULTRA3: U9.7 (CHAN2); also elsewhere on the board
ULTRA4: U9.6 (CHAN3); also elsewhere on the board
ULTRA5: U9.5 (CHAN4); also elsewhere on the board
ULTRA6: U9.4 (CHAN5); also elsewhere on the board
ULTRA7: U9.3 (CHAN6); also elsewhere on the board
ULTRA8: U9.2 (CHAN7); also elsewhere on the board
ULTRA9: U9.23 (CHAN8); also elsewhere on the board
ULTRA10: U9.22 (CHAN9); also elsewhere on the board
ULTRA11: U9.21 (CHAN10); also elsewhere on the board
ULTRA12: U9.20 (CHAN11); also elsewhere on the board
ULTRA13: U9.19 (CHAN12); also elsewhere on the board
ULTRA14: U9.18 (CHAN13); also elsewhere on the board
ULTRA15: U9.17 (CHAN14); also elsewhere on the board
ULTRA16: U9.16 (CHAN15); also elsewhere on the board
ULTRAS1: RJ45_RED.2; also elsewhere on the board
ULTRAS2: RJ45_RED.3; also elsewhere on the board
ULTRAS3: RJ45_RED.4; also elsewhere on the board
ULTRAS4: RJ45_RED.5; also elsewhere on the board
ULTRAS5: RJ45_RED.6; also elsewhere on the board
ULTRAS6: RJ45_RED.7; also elsewhere on the board
ULTRAS7: RJ45_WHITE.1; also elsewhere on the board
ULTRAS8: RJ45_WHITE.2; also elsewhere on the board
ULTRAS9: RJ45_WHITE.7; also elsewhere on the board
ULTRAS10: RJ45_WHITE.8; also elsewhere on the board
ULTRAS11: RJ45_BLUE.2; also elsewhere on the board
ULTRAS12: RJ45_BLUE.3; also elsewhere on the board
ULTRAS13: RJ45_BLUE.4; also elsewhere on the board
ULTRAS14: RJ45_BLUE.5; also elsewhere on the board
ULTRAS15: RJ45_BLUE.6; also elsewhere on the board
ULTRAS16: RJ45_BLUE.7; also elsewhere on the board
ULTRA_COM: U9.1 (COM); also elsewhere on the board
ULTRA_TRIGGER_1: Q10.2 (S), R19.2; also elsewhere on the board
ULTRA_TRIGGER_2: Q9.2 (S), R17.2; also elsewhere on the board
VCC: Q9.1 (G), Q10.1 (G), R17.1, R19.1, U9.24 (VCC); also elsewhere on the board

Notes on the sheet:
BLUE
WHITE
RED

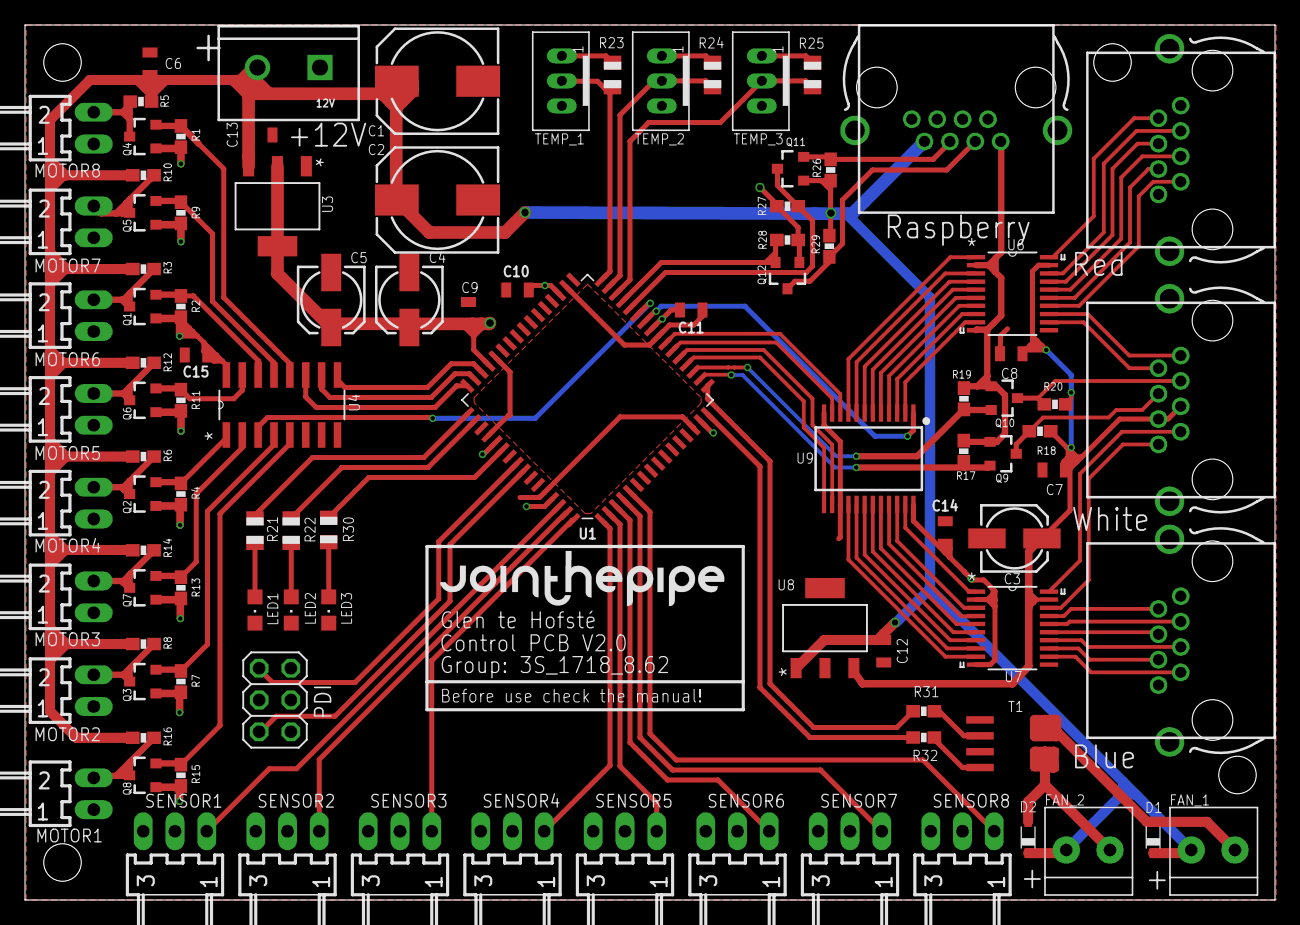
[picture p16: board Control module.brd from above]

Board: 2 copper layers, 100.0 x 70.0 mm, 99 parts (0 on the bottom side), 94 nets.

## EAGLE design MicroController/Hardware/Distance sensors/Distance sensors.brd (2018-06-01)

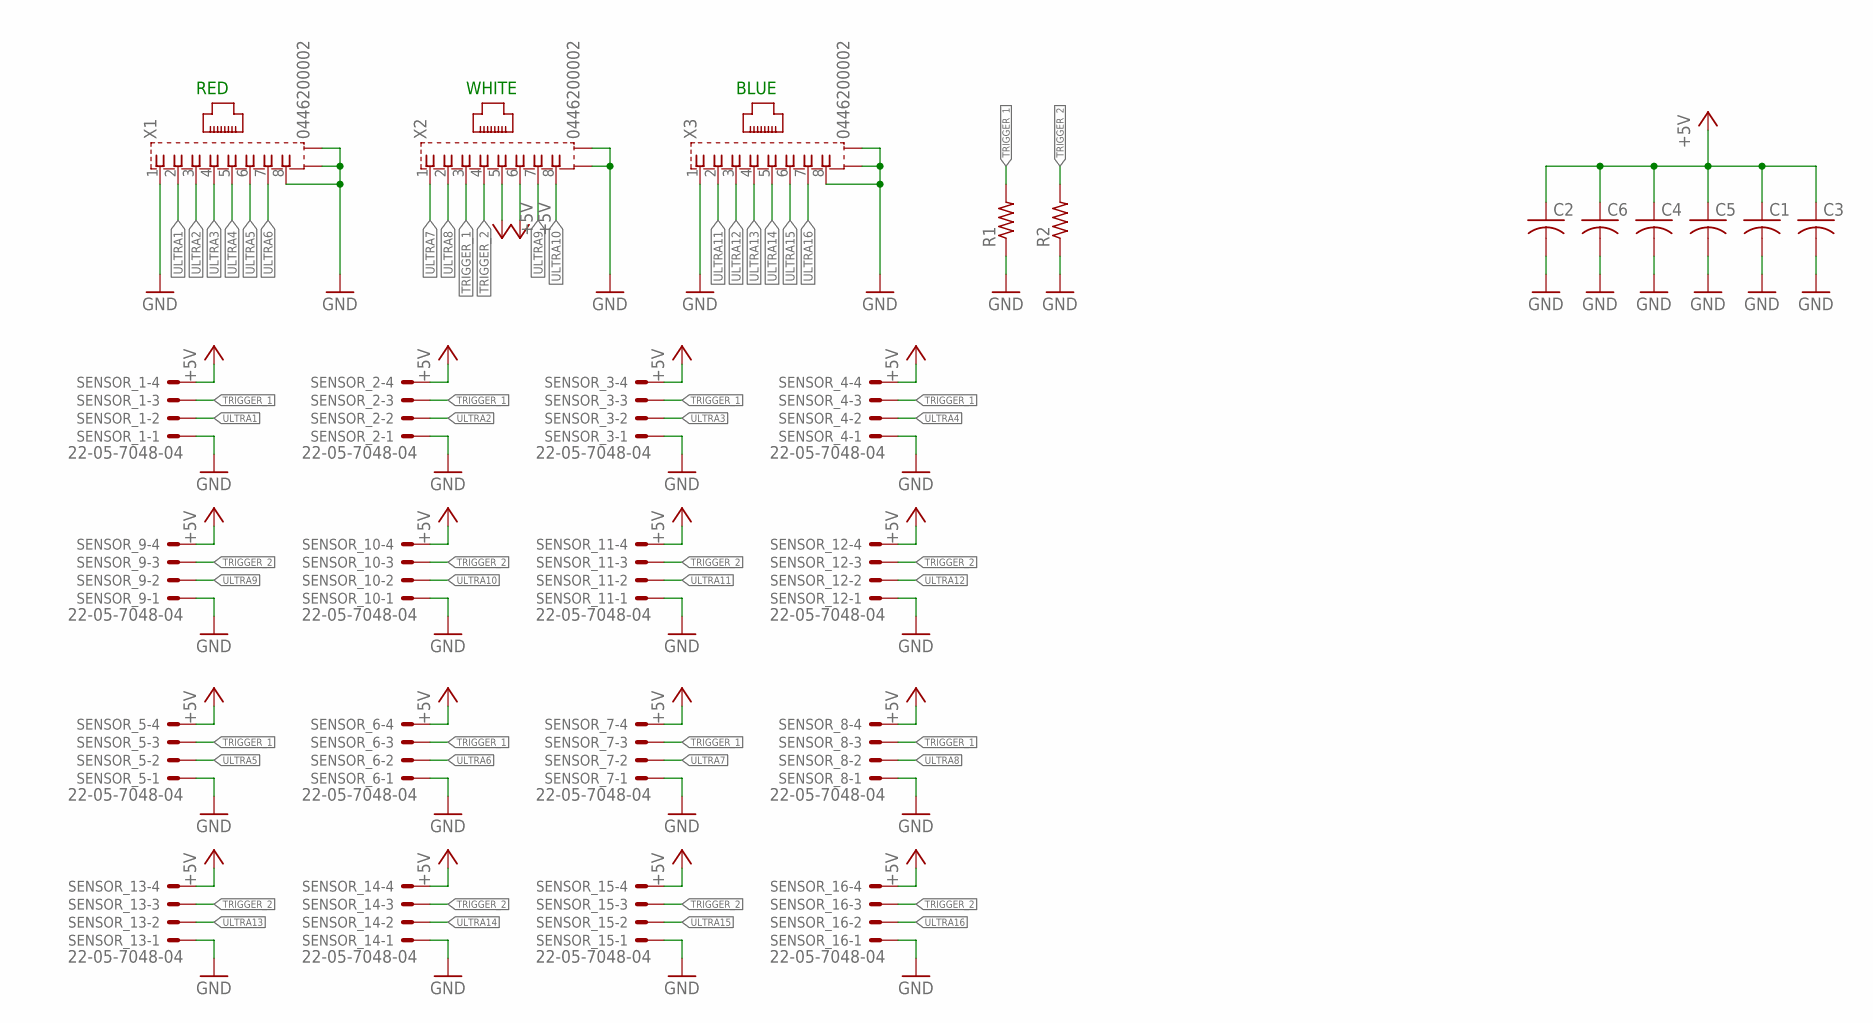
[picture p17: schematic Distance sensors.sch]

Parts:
C1, C2, C4, C5: C-USC0805; C0805
C3, C6: C-USC1206; C1206
R1, R2: R-US_R1206; R1206
SENSOR_1, SENSOR_2, SENSOR_3, SENSOR_4, SENSOR_5, SENSOR_6, SENSOR_7, SENSOR_8, SENSOR_9, SENSOR_10, SENSOR_11, SENSOR_12, SENSOR_13, SENSOR_14, SENSOR_15, SENSOR_16: 22-05-7048-04; 7395-04
X1, X2, X3: 0446200002

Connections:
+5V: C1.1, C2.1, C3.1, C4.1, C5.1, C6.1, SENSOR_1.4, SENSOR_2.4, SENSOR_3.4, SENSOR_4.4, SENSOR_5.4, SENSOR_6.4, SENSOR_7.4, SENSOR_8.4, SENSOR_9.4, SENSOR_10.4, SENSOR_11.4, SENSOR_12.4, SENSOR_13.4, SENSOR_14.4, SENSOR_15.4, SENSOR_16.4, X2.5, X2.6
GND: C1.2, C2.2, C3.2, C4.2, C5.2, C6.2, R1.1, R2.1, SENSOR_1.1, SENSOR_2.1, SENSOR_3.1, SENSOR_4.1, SENSOR_5.1, SENSOR_6.1, SENSOR_7.1, SENSOR_8.1, SENSOR_9.1, SENSOR_10.1, SENSOR_11.1, SENSOR_12.1, SENSOR_13.1, SENSOR_14.1, SENSOR_15.1, SENSOR_16.1, X1.1, X1.8, X1.S@1 (S1), X1.S@2 (S2), X2.S@1 (S1), X2.S@2 (S2), X3.1, X3.8, X3.S@1 (S1), X3.S@2 (S2)
TRIGGER_1: R1.2, SENSOR_1.3, SENSOR_2.3, SENSOR_3.3, SENSOR_4.3, SENSOR_5.3, SENSOR_6.3, SENSOR_7.3, SENSOR_8.3, X2.3
TRIGGER_2: R2.2, SENSOR_9.3, SENSOR_10.3, SENSOR_11.3, SENSOR_12.3, SENSOR_13.3, SENSOR_14.3, SENSOR_15.3, SENSOR_16.3, X2.4
ULTRA1: SENSOR_1.2, X1.2
ULTRA2: SENSOR_2.2, X1.3
ULTRA3: SENSOR_3.2, X1.4
ULTRA4: SENSOR_4.2, X1.5
ULTRA5: SENSOR_5.2, X1.6
ULTRA6: SENSOR_6.2, X1.7
ULTRA7: SENSOR_7.2, X2.1
ULTRA8: SENSOR_8.2, X2.2
ULTRA9: SENSOR_9.2, X2.7
ULTRA10: SENSOR_10.2, X2.8
ULTRA11: SENSOR_11.2, X3.2
ULTRA12: SENSOR_12.2, X3.3
ULTRA13: SENSOR_13.2, X3.4
ULTRA14: SENSOR_14.2, X3.5
ULTRA15: SENSOR_15.2, X3.6
ULTRA16: SENSOR_16.2, X3.7

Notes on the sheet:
WHITE
RED
BLUE

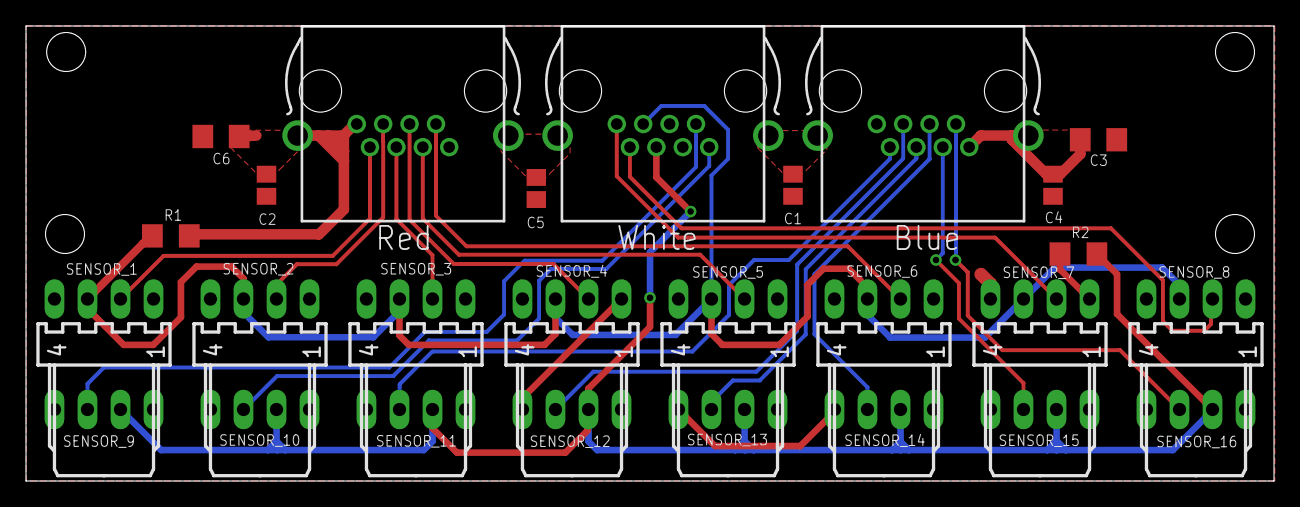
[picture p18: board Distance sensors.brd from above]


Board: 2 copper layers, 96.0 x 35.0 mm, 27 parts (8 on the bottom side), 20 nets.

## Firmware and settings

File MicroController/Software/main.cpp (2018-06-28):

/**
 * main.cpp
 *
 * Created: 06-Mar-18 11:56:46
 * Author: Robin C. Pel
 */


//// Includes
#include "includes.h"
#include "Hardware/SystemClock.h"
#include "Hardware/Gpio.h"
#include "Hardware/GenericTC.h"
#include "Master/RaspberryPi.h"
#include "Controllers/CoolingController.h"
#include "Controllers/MotorController.h"
#include "Sensors/DistanceSensor.h"


//// Namespaces
using namespace Hardware;
using namespace Communication;
using namespace Master;
using namespace Controllers;
using namespace Gpio;
using namespace Sensors;
using namespace TimerCounter;


//// LEDs
Pin greenLed = Pin::F3;                                                                                     // The green led
Pin yellowLed = Pin::F4;                                                                                    // The yellow led
Pin redLed = Pin::F6;                                                                                       // The red led
void runningLed( uint8_t ledVal ) { SetPinValue(greenLed, (Value) ledVal); }                                // This function controls the "running" LED, it will be on when the device is turned on
void busyLed( uint8_t ledVal ) { SetPinValue(yellowLed, (Value) ledVal); }                                  // This function controls the "busy" LED, it will be on when the device is processing a command
void errorLed( uint8_t ledVal ) { SetPinValue(redLed, (Value) ledVal); }                                    // This function controls the "error" LED, it will be on when an error has occurred


//// Raspberry Pi
RaspberryPi* raspberryPi;                                                                                   // The Raspberry Pi object
Usart::RxTx raspberrySerialPort = Usart::RxTx::D2_D3;                                                       // The Raspberry Pi's serial port pins


//// Cooling Controller Variables
CoolingController* coolingController;                                                                       // The cooling controller object
Pin temperatureSensorPins[3] = { Pin::D6, Pin::D5, Pin::D4 };                                               // The pins the temperature sensors are connected to
Pin fanGroupPins[2] = { Pin::C0, Pin::C1 };                                                                 // The pins the fan groups are connected to
TC coolingTc = TC::TC0C;                                                                                    // The timercounter the cooling controller uses


//// Motor Controller Variables
MotorController* motorController;                                                                           // The motor controller object
Pin rotationSensorPins[8] = { Pin::A0, Pin::A1, Pin::A2, Pin::A3, Pin::A4, Pin::A5, Pin::A6, Pin::A7 };     // The pins the rotation sensor are connected to
Pin motorMultiplexPins[3] = { Pin::F2, Pin::F1, Pin::F0 };                                                  // The pins the motor multiplexer is connected to
TC motorTimerCounter = TC::TC0D;                                                                            // The timercounter the motor controller uses
Pin motorTcPin = Pin::D1;                                                                                   // The pin the PWM signal has to be transmitted on for the motor controller


//// Distance Sensor
DistanceSensor* distanceSensor;                                                                             // The distance sensor object
Pin triggerPins[2] = { Pin::C3, Pin::C2 };                                                                  // The pins the distance sensors' triggers are connected to
Pin echoPin = Pin::D0;                                                                                      // The pin the distance sensors' echoes are connected to
Pin distanceMultiplexPins[4] = { Pin::C7, Pin::C6, Pin::C5, Pin::C4 };                                      // The pins the distance sensors' multiplexer is connected to
float emptyDistance = 105.0;                                                                                // After which distance a column is seen as "empty", can be changed using the "distance" command


//// Miscellaneous Variables
uint8_t const IDENTIFIER[] = { 0xAB, 0xBC, 0xCD, 0xDA };                                                    // The identifier bytes of the micro controller, these are used in the "sense" command
bool locked = false;                                                                                        // Boolean indicating whether the micro controller is locked or not
bool infiniteTest = true;                                                                                   // Boolean indicating whether to execute one test function endlessly or to go past more of them


//// Functions
// Lock all functionalities
void executeLockCommand(uint8_t* response)
{
    if (locked)
    {
        errorLed(1);                                                                                                    // Turn on the "error" LED
        response[0] = (uint8_t) RaspberryPi::ComException::Locked;                                                      // Add the "Locked" exception
        response[1] = 0x00;                                                                                             // Add the amount of parameters
    }
    else
    {
        locked = true;                                                                                                  // Lock the micro controller from doing anything but the "sense" and "unlock" command
        response[0] = (uint8_t) raspberryPi->getEquivalentCommandResponse(RaspberryPi::Command::Lock);                  // Add the equivalent command response
        response[1] = 0x00;                                                                                             // Add the amount of parameters
    }
}

// Unlock all functionalities
void executeUnlockCommand(uint8_t* response)
{
    locked = false;                                                                                                     // Unlock the micro controller so it will be able to execute all commands again
    response[0] = (uint8_t) raspberryPi->getEquivalentCommandResponse(RaspberryPi::Command::Unlock);                    // Add the equivalent command response
    response[1] = 0x00;                                                                                                 // Add the amount of parameters
}

// Return the constant identifier
void executeSenseCommand(uint8_t* response)
{
    response[0] = (uint8_t) raspberryPi->getEquivalentCommandResponse(RaspberryPi::Command::Sense);                     // Add the equivalent command response
    response[1] = 0x04;                                                                                                 // Add the amount of parameters
    
    response[2] = IDENTIFIER[0];                                                                                        // Add the first identifier byte
    response[3] = IDENTIFIER[1];                                                                                        // Add the second identifier byte
    response[4] = IDENTIFIER[2];                                                                                        // Add the third identifier byte
    response[5] = IDENTIFIER[3];                                                                                        // Add the fourth identifier byte
}

// Measure the temperatures and return them to the master
void executeTemperatureCommand(uint8_t* response, uint8_t* receivedCommand)
{
    if ( receivedCommand[1] == 1 ) coolingController->setLowerTargetTemperature(receivedCommand[2] / 2) ;           // Update the new target temperature (if supplied)
    coolingController->updateFanSpeed();
    
    response[0] = (uint8_t) raspberryPi->getEquivalentCommandResponse(RaspberryPi::Command::Temperature);           // Add the equivalent command response
    response[1] = 0x03;                                                                                             // Add the amount of parameters
    
    coolingController->gatherTemperatures();                                                                        // Refresh all t he temperature variables
    
    response[2] = (uint8_t) ( coolingController->getLowerTemperature() * 2.0 );                                     // Add the lower temperature to the response
    response[3] = (uint8_t) ( coolingController->getMiddleTemperature() * 2.0 );                                    // Add the middle temperature to the response
    response[4] = (uint8_t) ( coolingController->getUpperTemperature() * 2.0 );                                     // Add the upper temperature to the response
}

// Dispense one bottle from the selected column
void executeDispenseCommand(uint8_t* response, uint8_t* receivedCommand)
{
    if (locked)
    {
        errorLed(1);                                                                                                    // Turn on the "error" LED
        response[0] = (uint8_t) RaspberryPi::ComException::Locked;                                                      // Add the "Locked" exception
        response[1] = 0x00;                                                                                             // Add the amount of parameters
    }
    else
    {
        if ( (receivedCommand[1] == 0) || (receivedCommand[2] > 7) ) 
        {
            errorLed(1);                                                                                                // Turn on the "error" LED
            response[0] = (uint8_t) RaspberryPi::ComException::Parameter;                                               // Add the "Not enough or wrong parameters" exception
            response[1] = 0x00;                                                                                         // Add the amount of parameters
        }
        else
        {
            response[0] = (uint8_t) raspberryPi->getEquivalentCommandResponse(RaspberryPi::Command::Dispense);          // Add the equivalent command response
            response[1] = 0x01;                                                                                         // Add the amount of parameters
            
            motorController->rotateMotor(receivedCommand[2]);                                                           // Rotate the requested motor
            
            // Do this two times, it looks like the distance sensors sometimes need to "warm up"
            response[2] = distanceSensor->getSimpleData(emptyDistance);                                                 // Add the empty state of all eight columns
            response[2] = distanceSensor->getSimpleData(emptyDistance);                                                 // Add the empty state of all eight columns
        }
    }
}

// Measure the distances in all columns and return whether the the columns are empty or not
void executeDistanceCommand(uint8_t* response, uint8_t* receivedCommand)
{
    if ( receivedCommand[1] > 1 )
    {
        errorLed(1);                                                                                                // Turn on the "error" LED
        response[0] = (uint8_t) RaspberryPi::ComException::Parameter;                                               // Add the "Not enough or wrong parameters" exception
        response[1] = 0x00;                                                                                         // Add the amount of parameters
    }
    else
    {
        if ( receivedCommand[1] == 1 ) emptyDistance = receivedCommand[2];                                          // Update the empty distance (if supplied)
        
        response[0] = (uint8_t) raspberryPi->getEquivalentCommandResponse(RaspberryPi::Command::Distance);          // Add the equivalent command response
        response[1] = 0x01;                                                                                         // Add the amount of parameters
        
        // Do this two times, it looks like the distance sensors sometimes need to "warm up"
        response[2] = distanceSensor->getSimpleData(emptyDistance);                                                 // Add the empty state of all eight columns
        response[2] = distanceSensor->getSimpleData(emptyDistance);                                                 // Add the empty state of all eight columns
    }
}

// Execute a command
void executecommand(uint8_t* response, uint8_t* receivedCommand)
{
    switch ((RaspberryPi::Command) receivedCommand[0])
    {
        case RaspberryPi::Command::Lock:                executeLockCommand(response);                                   break;      // Received a lock command
        case RaspberryPi::Command::Unlock:              executeUnlockCommand(response);                                 break;      // Received an unlock command
        case RaspberryPi::Command::Sense:               executeSenseCommand(response);                                  break;      // Received a sense command
        case RaspberryPi::Command::Temperature:         executeTemperatureCommand(response, receivedCommand);           break;      // Received a temperature command
        case RaspberryPi::Command::Dispense:            executeDispenseCommand(response, receivedCommand);              break;      // Received a dispense command
        case RaspberryPi::Command::Distance:            executeDistanceCommand(response, receivedCommand);              break;      // Received a distance command
        default:                                                                                                        break;      // Impossible
    }
}

// Wait for a command, execute the command, return the response, do it all again
void runRoutine(void)
{
    while (1)
    {
        uint8_t operationStatus = raspberryPi->waitForNextCommand();        // 0 = success, 1 = command does not exist, 2 = timeout
        uint8_t* receivedCommand = raspberryPi->getCommand();               // Get the location to the received command
        uint8_t response[6] = { 0 };                                        // The response will never be larger than six bytes
        
        busyLed(1);
        
        switch (operationStatus)
        {
            case 0:     // Everything went fine, the command is recognized and there was no timeout
            executecommand(response, receivedCommand);
            break;
            
            
            case 1:     // Command does not exist
            errorLed(1);
            response[0] = (uint8_t) RaspberryPi::ComException::Unknown;     // Add the "Command Unknown" Exception as command response
            response[1] = 0x00;                                             // Zero parameters
            break;
            
            
            case 2:     // Timeout
            errorLed(1);
            response[0] = (uint8_t) RaspberryPi::ComException::TimeOut;     // Add the "Serial timeout" Exception as command response
            response[1] = 0x00;                                             // Zero parameters
            break;
        }
        
        raspberryPi->returnResponse(response);                              // Return the response
        
        busyLed(0);
        errorLed(0);
    }
}

// Set the correct clock source, initialize the generic timer-counter, initialize the LEDs
void initialize(void)
{
    // Initialize the system clock and the generic timer-counter
    SystemClock::SetClockSource(SystemClock::Source::RC32MHz);
    TimerCounter::InitializeGenericTC();
    
    // Initialize the status LEDs
    SetPinDirection(greenLed, Dir::Output);
    SetPinDirection(yellowLed, Dir::Output);
    SetPinDirection(redLed, Dir::Output);
}

// Initialize the raspberry pi, cooling controller, motor controller and distance sensor objects
void initializeHardware(void) 
{
    // Initialize all the other hardware
    raspberryPi = new RaspberryPi(raspberrySerialPort);
    coolingController = new CoolingController(temperatureSensorPins, fanGroupPins, coolingTc);
    motorController = new MotorController(motorMultiplexPins, motorTimerCounter, motorTcPin, rotationSensorPins);
    distanceSensor = new DistanceSensor(triggerPins, echoPin, distanceMultiplexPins);
}

// Raspberry Pi test command
void raspiTestCommand(uint8_t* response, uint8_t* receivedCommand)
{
    static uint8_t dispenseStatus = 0;
    response[0] = (uint8_t) raspberryPi->getEquivalentCommandResponse((RaspberryPi::Command) receivedCommand[0]);
    
    switch ((RaspberryPi::Command) receivedCommand[0])
    {
        case RaspberryPi::Command::Sense:       response[1] = 0x04; response[2] = IDENTIFIER[0]; response[3] = IDENTIFIER[1]; response[4] = IDENTIFIER[2]; response[5] = IDENTIFIER[3]; break;
        case RaspberryPi::Command::Dispense:    response[1] = 0x01; response[2] = ( dispenseStatus++ % 2 ); break;
        case RaspberryPi::Command::Distance:    response[1] = 0x01; response[2] = 0x03; break;
        case RaspberryPi::Command::Temperature:
        default:                                response[1] = 0x00;
    }
}

// Raspberry Pi test mode
void testRaspi(void) 
{
    // Initialize the system clock and the generic timer-counter
    SystemClock::SetClockSource(SystemClock::Source::RC32MHz);
    TimerCounter::InitializeGenericTC();
    
    // Initialize all the other hardware
    raspberryPi = new RaspberryPi(raspberrySerialPort);
    
    while (1)
    {
        uint8_t operationStatus = raspberryPi->waitForNextCommand();        // 0 = success, 1 = command does not exist, 2 = timeout
        uint8_t* receivedCommand = raspberryPi->getCommand();               // Get the location to the received command
        uint8_t response[6] = { 0 };                                        // The response will never be larger than six bytes
        
        switch (operationStatus)
        {
            case 0:     // Everything went fine, the command is recognized and there was no timeout
            raspiTestCommand(response, receivedCommand);
            break;
            
            
            case 1:     // Command does not exist
            errorLed(1);
            response[0] = (uint8_t) RaspberryPi::ComException::Unknown;     // Add the "Command Unknown" Exception as command response
            response[1] = 0x00;                                             // Zero parameters
            break;
            
            
            case 2:     // Timeout
            errorLed(1);
            response[0] = (uint8_t) RaspberryPi::ComException::TimeOut;     // Add the "Serial timeout" Exception as command response
            response[1] = 0x00;                                             // Zero parameters
            break;
        }
        
        raspberryPi->returnResponse(response);                              // Return the response
    }
}

// Rotate all the motors
void testMotors(void) 
{
    do
    {
        for (int i = 0; i < 8; i++)
        {
            busyLed(1);
            motorController->rotateMotor(i);
            _delay_ms(1000);
            busyLed(0);
            _delay_ms(1000);
        }
    } while (infiniteTest);
}

// Test both fan groups
void testFans(void) 
{
    busyLed(1);
        
    coolingController->setFangroupSpeed(0, 25);         // Lower fans
    coolingController->setFangroupSpeed(1, 25);         // Upper fans
    
    while (infiniteTest);
    busyLed(0);
    
    //do 
    //{
        //busyLed(1);
        //
        //coolingController->setFangroupSpeed(0, 100);
        //coolingController->setFangroupSpeed(1, 100);
        //_delay_ms(5000);
        //coolingController->setFangroupSpeed(0, 0);
        //coolingController->setFangroupSpeed(1, 0);
        //_delay_ms(5000);
        //
        //busyLed(0);
    //} while (infiniteTest);
    
}

// Test the temperature sensors
void temperatureCheckTest(void) 
{
    do
    {
        busyLed(1);
        
        volatile float temperatures[3] = { 50.0 };
        
        coolingController->gatherTemperatures();
        
        temperatures[0] = coolingController->getLowerTemperature();
        temperatures[1] = coolingController->getMiddleTemperature();
        temperatures[2] = coolingController->getUpperTemperature();
        
        busyLed(0);
    } while (infiniteTest);
}

// Test the distance sensors
void testDistSensor(void) 
{
    //  00  01  02  03  04  05  06  07
    // [08][01][10][03][12][05][14][07]
    // [00][09][02][11][04][13][06][15]
    
    do 
    {
        busyLed(1);
        
        //volatile uint8_t emptyStatuss = distanceSensor->getSimpleData(emptyDistance);
        
        volatile float distances[16] = { 0.0 };
        float* resultLocation = distanceSensor->getData();
        
        for (int i = 0; i < 16; i++)
            distances[i] = resultLocation[i];
        
        const int sensorNo = 5;
        
        //for (int i = sensorNo; i < (sensorNo+1); i++)
            //distances[i] = distanceSensor->getOneData(i);
        
        busyLed(0);
    } while (infiniteTest);
}

// The general main
int main()
{
    initialize();               // Initialize the base system
    initializeHardware();       // Initialize the other hardware
    runningLed(1);              // Turn on the "running" LED
    runRoutine();               // Start the routine
    runningLed(0);              // The "running" LED should never be stopped since the "runRoutine" function will run endlessly
    
    
    //testRaspi();
    //testMotors();
    //testFans();
    //temperatureCheckTest();
    //testDistSensor();
    
}

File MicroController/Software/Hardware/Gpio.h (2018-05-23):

/* 
* Gpio.h
*
* Created: 20-Mar-18 11:07:31
* Author: Robin C. Pel
*/

#ifndef __GPIO_H__
#define __GPIO_H__

#include <stdint.h>
#include <avr/io.h>

namespace Hardware 
{
	namespace Gpio 
	{
		// Ports
		enum class Port
		{
			PortA,
			PortB,
			PortC,
			PortD,
			PortE,
			PortF,
			PortR
		};
		
		// Pin numbers
		enum class PinNo
		{
			Pin0,
			Pin1,
			Pin2,
			Pin3,
			Pin4,
			Pin5,
			Pin6,
			Pin7
		};
		
		// Pin - consist out of a port and pin number
		enum class Pin
		{
			A0 = ((uint8_t) Port::PortA << 3) + (uint8_t) PinNo::Pin0,
			A1 = ((uint8_t) Port::PortA << 3) + (uint8_t) PinNo::Pin1,
			A2 = ((uint8_t) Port::PortA << 3) + (uint8_t) PinNo::Pin2,
			A3 = ((uint8_t) Port::PortA << 3) + (uint8_t) PinNo::Pin3,
			A4 = ((uint8_t) Port::PortA << 3) + (uint8_t) PinNo::Pin4,
			A5 = ((uint8_t) Port::PortA << 3) + (uint8_t) PinNo::Pin5,
			A6 = ((uint8_t) Port::PortA << 3) + (uint8_t) PinNo::Pin6,
			A7 = ((uint8_t) Port::PortA << 3) + (uint8_t) PinNo::Pin7,
			B0 = ((uint8_t) Port::PortB << 3) + (uint8_t) PinNo::Pin0,
			B1 = ((uint8_t) Port::PortB << 3) + (uint8_t) PinNo::Pin1,
			B2 = ((uint8_t) Port::PortB << 3) + (uint8_t) PinNo::Pin2,
			B3 = ((uint8_t) Port::PortB << 3) + (uint8_t) PinNo::Pin3,
			B4 = ((uint8_t) Port::PortB << 3) + (uint8_t) PinNo::Pin4,
			B5 = ((uint8_t) Port::PortB << 3) + (uint8_t) PinNo::Pin5,
			B6 = ((uint8_t) Port::PortB << 3) + (uint8_t) PinNo::Pin6,
			B7 = ((uint8_t) Port::PortB << 3) + (uint8_t) PinNo::Pin7,
			C0 = ((uint8_t) Port::PortC << 3) + (uint8_t) PinNo::Pin0,
			C1 = ((uint8_t) Port::PortC << 3) + (uint8_t) PinNo::Pin1,
			C2 = ((uint8_t) Port::PortC << 3) + (uint8_t) PinNo::Pin2,
			C3 = ((uint8_t) Port::PortC << 3) + (uint8_t) PinNo::Pin3,
			C4 = ((uint8_t) Port::PortC << 3) + (uint8_t) PinNo::Pin4,
			C5 = ((uint8_t) Port::PortC << 3) + (uint8_t) PinNo::Pin5,
			C6 = ((uint8_t) Port::PortC << 3) + (uint8_t) PinNo::Pin6,
			C7 = ((uint8_t) Port::PortC << 3) + (uint8_t) PinNo::Pin7,
			D0 = ((uint8_t) Port::PortD << 3) + (uint8_t) PinNo::Pin0,
			D1 = ((uint8_t) Port::PortD << 3) + (uint8_t) PinNo::Pin1,
			D2 = ((uint8_t) Port::PortD << 3) + (uint8_t) PinNo::Pin2,
			D3 = ((uint8_t) Port::PortD << 3) + (uint8_t) PinNo::Pin3,
			D4 = ((uint8_t) Port::PortD << 3) + (uint8_t) PinNo::Pin4,
			D5 = ((uint8_t) Port::PortD << 3) + (uint8_t) PinNo::Pin5,
			D6 = ((uint8_t) Port::PortD << 3) + (uint8_t) PinNo::Pin6,
			D7 = ((uint8_t) Port::PortD << 3) + (uint8_t) PinNo::Pin7,
			E0 = ((uint8_t) Port::PortE << 3) + (uint8_t) PinNo::Pin0,
			E1 = ((uint8_t) Port::PortE << 3) + (uint8_t) PinNo::Pin1,
			E2 = ((uint8_t) Port::PortE << 3) + (uint8_t) PinNo::Pin2,
			E3 = ((uint8_t) Port::PortE << 3) + (uint8_t) PinNo::Pin3,
			E4 = ((uint8_t) Port::PortE << 3) + (uint8_t) PinNo::Pin4,
			E5 = ((uint8_t) Port::PortE << 3) + (uint8_t) PinNo::Pin5,
			E6 = ((uint8_t) Port::PortE << 3) + (uint8_t) PinNo::Pin6,
			E7 = ((uint8_t) Port::PortE << 3) + (uint8_t) PinNo::Pin7,
			F0 = ((uint8_t) Port::PortF << 3) + (uint8_t) PinNo::Pin0,
			F1 = ((uint8_t) Port::PortF << 3) + (uint8_t) PinNo::Pin1,
			F2 = ((uint8_t) Port::PortF << 3) + (uint8_t) PinNo::Pin2,
			F3 = ((uint8_t) Port::PortF << 3) + (uint8_t) PinNo::Pin3,
			F4 = ((uint8_t) Port::PortF << 3) + (uint8_t) PinNo::Pin4,
			F5 = ((uint8_t) Port::PortF << 3) + (uint8_t) PinNo::Pin5,
			F6 = ((uint8_t) Port::PortF << 3) + (uint8_t) PinNo::Pin6,
			F7 = ((uint8_t) Port::PortF << 3) + (uint8_t) PinNo::Pin7,
			R0 = ((uint8_t) Port::PortR << 3) + (uint8_t) PinNo::Pin0,
			R1 = ((uint8_t) Port::PortR << 3) + (uint8_t) PinNo::Pin1
		};
		
		// Pin Directions
		enum class Dir
		{
			Input,
			Output
		};
	
		// Pin Values
		enum class Value
		{
			Low,
			High
		};
	
		// Pin Modes
		enum class Mode
		{
			Totem			= 0b00000000,
			BusKeeper		= 0b00001000,
			PullDown		= 0b00010000,
			PullUp			= 0b00011000,
			WiredOr			= 0b00100000,
			WiredAnd		= 0b00101000,
			WiredOrPullDown	= 0b00110000,
			WiredAndPullUp	= 0b00111000
		};
		
		
		// Functions
		void SetPinDirection(Pin pin, Dir dir);                 // Configure the given direction on the given pin
		void TogglePinDirection(Pin pin);                       // Toggle the direction on the given pin
		void SetPinValue(Pin pin, Value val);                   // Set the given value on the given pin
        Value GetPinValue(Pin pin);                             // Get the value of the given pin
		void TogglePinValue(Pin pin);                           // Toggle the value of the given pin
		void SetPinMode(Pin pin, Mode mode);                    // Configure the given mode on the given pin
		PORT_t* GetPort(Pin pin);                               // Get a pointer to the port of the given pin
		PinNo GetPinNumber(Pin pin);                            // Get the pin number of the given pin
		register8_t* GetPinConfigReg(Pin pin);                  // Get the pin configuration register of the given pin
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

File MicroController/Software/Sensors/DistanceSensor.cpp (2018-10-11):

/*
* DistanceSensor.cpp
*
* Created: 19-Mar-18 14:38:47
* Author: Robin C. Pel
*/

#include "DistanceSensor.h"

// Precision calculation (cm/tick) = (1 / ((F_CPU / Presc) / 1000000)) / 58
// Presc =  256:   0.13793103448 cm/tick
// Presc = 1024:   0.55172413793 cm/tick

/* Columns Layout (Top view, from the front):
 * 
 * ColumnNo:             00  01  02  03  04  05  06  07
 * ColumnSectionNo:     [08][01][10][03][12][05][14][07]
 * ColumnSectionNo:     [00][09][02][11][04][13][06][15]
 *
 * [00] t/m [07] --> Trigger 0
 * [08] t/m [15] --> Trigger 1
 * 
 */

Sensors::DistanceSensor::DistanceSensor(Gpio::Pin* triggerPins, Gpio::Pin echoPins, Gpio::Pin* multiplexPins) 
{
    for (int i = 0; i < 2; i++) 
    {
        triggerPin[i] = triggerPins[i];
        Gpio::SetPinDirection(triggerPin[i], Gpio::Dir::Output);        // Configure the trigger pins as output
    }        
    
    echoPin = echoPins;
    Gpio::SetPinDirection(echoPin, Gpio::Dir::Input);                   // Configure the echo pin as input
     
    for (int i = 0; i < 4; i++) 
    {
        multiplexPin[i] = multiplexPins[i];
        Gpio::SetPinDirection(multiplexPin[i], Gpio::Dir::Output);      // Configure the mux pins as output
    }
}

float* Sensors::DistanceSensor::getData()
{
    for (int i = 0; i < 16; i++) 
    {
        if (i != 5 && i != 14 && i != 12)
            buffer[i] = getDistance(i);         // Get the distance of each sensor
        _delay_ms(40);                      // Wait a bit to make sure trigger 0 and trigger 1 do not get mixed
    }
    
    return (float*) buffer;                 // Return a pointer which points to where the read data is stored
}

float Sensors::DistanceSensor::getOneData(uint8_t channel) 
{
    return getDistance(channel);
}

uint8_t Sensors::DistanceSensor::getSimpleData(float emptyDistance)
{
    uint8_t simpleData = 0b00000000;
    getData();
    
    // Check every column
    for (int i = 0; i < 8; i++) 
    {
        if ( (buffer[i] > emptyDistance) || (buffer[i+8] > emptyDistance) )     // Every column consists out of two column sections, an even and an odd section. We need to check them both!
            simpleData |= ( 1 << i );                                           // Bit-shift the column status to the correct bit
    }     // i will try to take one raw out of the sensors and make use of only one sensor for two c.s. 
	//try to fix the empty distance  variable 
	//if ( ( buffer[i] > emptyDistance))
	//simpleData |=(1 <<i); figure out a way to use the loop between 2 0 4 6 9 11 13 15
    
    return simpleData;
}

void Sensors::DistanceSensor::setMuxChannel(uint8_t channel)
{
    for (int i = 0; i < 4; i++)
        Gpio::SetPinValue(multiplexPin[i], (Gpio::Value) (( channel >> i ) & 0b1));
    
    _delay_ms(1);       // Just to be sure the multiplexer has switched its channel we'll wait for one millisecond
}

void Sensors::DistanceSensor::sendTtl(Gpio::Pin pin)
{
    Gpio::SetPinValue(pin, Gpio::Value::High);      // Set the pin high
    _delay_us(15);                                  // For 15 microseconds
    Gpio::SetPinValue(pin, Gpio::Value::Low);       // And set it low again
}

uint16_t Sensors::DistanceSensor::getPulseWidth(Gpio::Pin pin)
{
    while (Gpio::GetPinValue(pin) == Gpio::Value::Low);                 // Wait for the pin to go high
    TimerCounter::ClearCount(TimerCounter::GetGenericTC());             // Clear the counter
    while (Gpio::GetPinValue(pin) == Gpio::Value::High);                // Wait for the pin to go low
    return TimerCounter::GetCount(TimerCounter::GetGenericTC());        // Return how long the signal was high aka the "pulse width"
}

float Sensors::DistanceSensor::ticksToCentimeters(uint16_t prescval, uint16_t ticks)
{
    float us = TimerCounter::TicksToMicoSeconds(prescval, ticks);       // Convert the amount of ticks to microseconds
    return us / 58.0;                                                   // Calculate the distance in centimeters
}

float Sensors::DistanceSensor::getDistance(uint8_t columnSectionNo)
{
    setMuxChannel(columnSectionNo);                     // Set the correct mux channel
    
    if (columnSectionNo > 7) sendTtl(triggerPin[1]);    // Send the TTL to trigger 1
    else sendTtl(triggerPin[0]);                        // Send the TTL to trigger 0
    
    uint16_t echo = getPulseWidth(echoPin);             // Get the width of the pulse
    return ticksToCentimeters(1024, echo);              // Return the measured distance in centimeters
}

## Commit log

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2018-03-09 Started a clean project for the control module
    This module will consists of the microcontroller and all the necessary components needed to make this board function as a proper control module. This module will in the final result communicate with 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
    [Control module.sch]
2018-03-12 Added first IC logic components
    Added the ATXMEGA256A3 microcontroller, the CD74HC4067 16 channel (de)multiplexer and the CD4051BM 8 channel (de)multiplexer.
    [Control module.sch]
2018-03-12 Added level shifting logic
    The stepper motor drivers require a larger voltage than the microcontroller can deliver. For redundancy this voltage will be higher than 5 volts.
    [Control module.sch]
2018-03-12 Created a board file
    This will be the design of the PCB.
    [Control module.brd]
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2018-03-22 Added two more classes, the AtxMega class and the SystemClock class. AtxMega's only purpose - for now - is to simplify the changing of the "Configuration Change Protection" modes. SystemClock on the 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
    [Gpio.cpp, Gpio.h, main.cpp]
2018-03-22 Changed many things in the layout.
    Added more I/O and connectivity to the Raspberry Pi.
    [Control module.brd, Control module.sch]
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2018-03-28 Major improvements
    The Ultrasone PCB is in a good place now, it has also been well implemented on the control PCB.
    [Control module.brd, Control module.sch, Distance sensors.brd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]
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2018-04-03 Added the temperature sensors
    Also changed a lot of connections and PCB traces.
    [Control module.brd, Control module.sch]
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2018-04-06 Added the hardware that makes the TTL line of a higher voltage.
    [Control module.brd, Control module.sch]
2018-04-09 Changed some minor things to make the PCB less expensive to produce.
    Also the RX TX is now of a higher voltage. This should make the communication less susceptible to noise.
    [Control module.brd]
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2018-04-10 The version that is ordered at Eurocircuits.
    The full version of the microcontroller PCB, revision 1.
    [Control module.brd, Control module.sch]
2018-04-11 Started a redesign of the Distance sensor PCB.
    [Control module.sch, Distance sensors.brd, Distance sensors.sch]
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2018-04-13 Many changes to the Ultrasone sensor PCB.
    Added a lot op components.
    [Distance sensors.brd, Distance sensors.sch]
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2018-04-18 Created a new project for the Raspberry Pi PCB
    The PCB will be connected to the Raspberry using a band cable, as it is often done. This makes replacing components easy and the Raspberry re-usable.
    [Raspberry Pi PCB.brd, Raspberry Pi PCB.sch]
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2018-04-23 Started working on the next revision of the Control PCB.
    Work in progress. The notes on the hardware can be found in the documentation.
    [Control module.brd, Control module.sch]
2018-04-26 Control PCB revision 2 is now complete.
    A lot of changes compared to the first revision. Most noticable the layout of the connectors and the addition of the motor driver.
    [Control module.brd, Control module.sch]
2018-05-07 Final check before ordering the Control module PCB.
    Small changes on the soldermask. No component changes.
    [Control module.brd]
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2018-05-08 The distance sensor PCB is close to finished.
    There needs to be a final check before ordering the PCB. The PCB is not very complicated compared to the previous version, making it easier to check.
    [Distance sensors.brd, Distance sensors.sch]
2018-05-09 Power component changes.
    The planned buck converter will not be used on the PCB. It was decided that an AC/DC converter will be used that was available from the first Bidon dispenser project. This converter already outputs t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
    [Raspberry Pi PCB.brd, Raspberry Pi PCB.sch]
2018-05-14 Added a step up converter.
    This step up is required for the 12 volt data communication between the Raspberry and the microcontroller. It ofcourse also works with the lower 5 volt, but for reliability we use 12 volt.
    [Raspberry Pi PCB.brd, Raspberry Pi PCB.sch]
2018-05-16 Many changes to the PCB design.
    Most of the required components have now been included.
    [Raspberry Pi PCB.brd, Raspberry Pi PCB.sch]
2018-05-16 Removed the step up converter.
    After some testing I found out that the voltage that is provided by the control PCB would be sufficient for the level conversion. This means that no boost converter is required.
    [Raspberry Pi PCB.brd, Raspberry Pi PCB.sch]
2018-05-17 Added a connector for the reed switch.
    The reed switch is used to detect if the door is open. It works in combination with a magnet that is placed on the case itself.
    [Raspberry Pi PCB.brd, Raspberry Pi PCB.sch]
2018-05-17 Finished the first version of the Raspberry PCB.
    Design rule check worked out fine. The PCB should now be ready for ordering.
    [Raspberry Pi PCB.brd, Raspberry Pi PCB.sch]
2018-05-19 Added a lot of stuff:
    A "Pn532" class has been added to keep all of the NFC stuff in one place.
    This class is still very minimalistic and is neither bug free, at the moment of writing this I cannot get an ACK back from the PN532 ("0x00 0x00 0xff 0x00 0xff" I believe).
    Also added some images, these will be shown on the promotional part of the screen.
    At this stage of the project the code is pretty lackluster in terms of comments, these will be added later on down the line.
2018-05-22 The Raspberry PCB is almost finished now.
    The buttons and the jumper has been included. The size has been increased. All the primary functionality has been finished now.
    [Raspberry Pi PCB.brd, Raspberry Pi PCB.sch]
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2018-05-24 Added the image source which will show which button corresponds to which bottle colour. Removed the two test timers and replaced them with one timer which gets triggered every 100ms, not only will th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
2018-05-25 Fixed a few bugs in the microcontroller code. Added an example of how to use the "Raspberry Pi" class.
    Commented out the gif for now, showing it costed a lttle bit too much CPU power to my liking, it also slowed down the promotion timer somehow.
    Changed the UI a bit, added some button for command testing to the microcontroller.
    Removed some old Serial test code.
    Finished the "Microcontroller" class.
    [RaspberryPi.h, main.cpp]
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2018-05-28 Added some values to the components.
    These are handy when generating the BOM file.
    [Raspberry Pi PCB.brd, Raspberry Pi PCB.sch]
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2018-05-30 Started on removing the sensor class. Also updated the distance sensor class a bit to work correctly with the system.
    [DistanceSensor.cpp, RotationSensor.cpp]
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2018-05-31 Tested the motorcontroller, it works! Replaced the ledcontroller with functions in the main. Some minor changes in the distance sensor.
    [DistanceSensor.cpp, MotorController.cpp, main.cpp]
2018-05-31 Added some more comments here and there. Filled in most of the coolingcontroller class except for the "updateFanSpeed" method. Fixed a small bug in the motorcontroller where it would always pick the 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
    [CoolingController.cpp, CoolingController.h, MotorController.cpp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]
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2018-06-05 Tested the distance sensors with the final setup. Changed the order of the distance sensors so their "echo" signals won't get mixed.
    [DistanceSensor.cpp, main.cpp]
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2018-06-06 Started on implementing a Mutex so the serial port won't be spammed with data. Added the door sensor and timers to the "unloadMainPage" function so everything will be cleaned up nicely when the progr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
2018-06-06 Added a few methods to the cooling controller class for testing purposes. Fixed a pretty embarrassing bug in the onewire class. Added a temperature test function in the main.
    [CoolingController.cpp, CoolingController.h, OneWire.cpp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]
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2018-06-07 Replaced the "temperature check" command with the "temperature" command. Added a "send command" function.
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2018-06-11 Many changes in this new version of the Control PCB.
    The motor drivers are replaced by MOSFET's.
    The schematic is much better organized.
    Small additional changes.
    [Control module.brd, Control module.sch]
2018-06-12 Finished the Control PCB version 2.0
    Not a lot of changes where made comparing to the previous version of the PCB. Most noticeably the way the fans are controlled has changed. Further some small things that where found out during tests 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
    [Control module.brd, Control module.sch]
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2018-06-18 Replaced the mutex in the "microcontroller" class by a semaphore. Added a I2C PN532 class to test wether this works better than SPI or not.
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2018-06-22 Fixed a pretty embarrassing bug in the Gpio class. Updated the protocol description. Made the lower target temperature configurable again. Removed the ugly ADC code from the motorController and repla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
    [DistanceSensor.cpp, Gpio.cpp, MotorController.cpp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]
2018-06-25 Fixed a bug in the microcontroller's distance command. Added the overlay to show which bottles are out of stock. Added the bindings to trigger an update of the UI when a bottle's status changes. Edit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
    [main.cpp]
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2018-10-11 commented out three broken ultra sonic sensors from the loop
    [DistanceSensor.cpp]

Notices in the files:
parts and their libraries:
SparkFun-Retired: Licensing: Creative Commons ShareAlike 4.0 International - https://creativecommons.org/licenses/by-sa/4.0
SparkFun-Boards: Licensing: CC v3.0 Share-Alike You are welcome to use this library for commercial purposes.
